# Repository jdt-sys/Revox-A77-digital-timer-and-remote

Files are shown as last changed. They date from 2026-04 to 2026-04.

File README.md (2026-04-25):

# Revox A77 Digital Counter + Web Remote

Adds a digital tape counter and web-based remote control to a Revox A77.  
All mods are reversible and use existing holes where possible.

## Features

- Digital tape counter (OLED display)  
- Web-based remote control (WiFi)  
- Real-time counter updates over WebSocket  
- Safe transport control logic (no rewind → play abuse)  
- Non-invasive install  

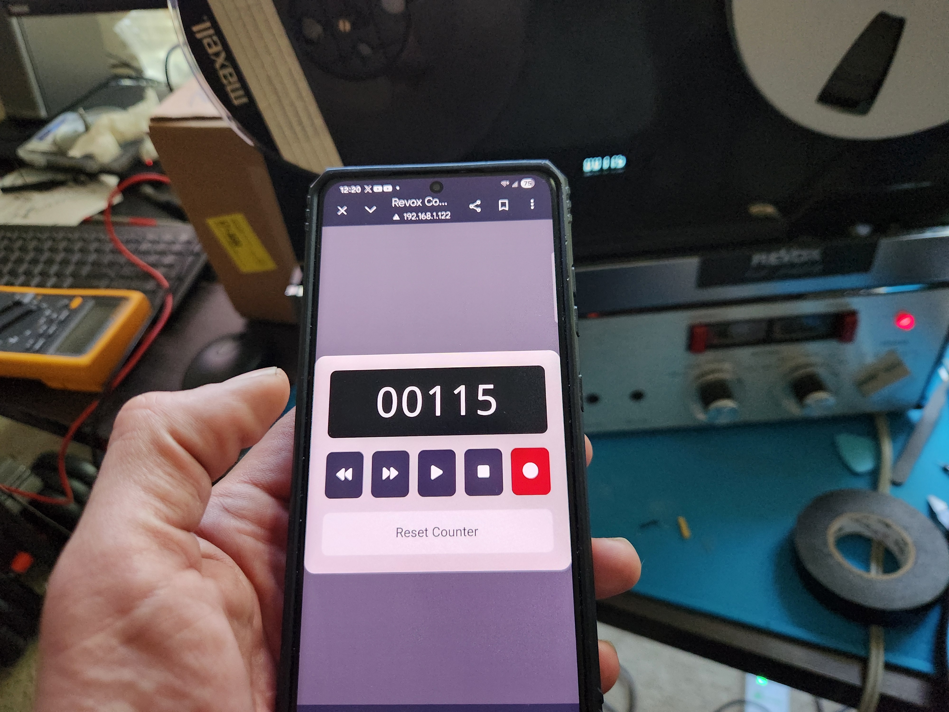
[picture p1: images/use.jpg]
Web UI


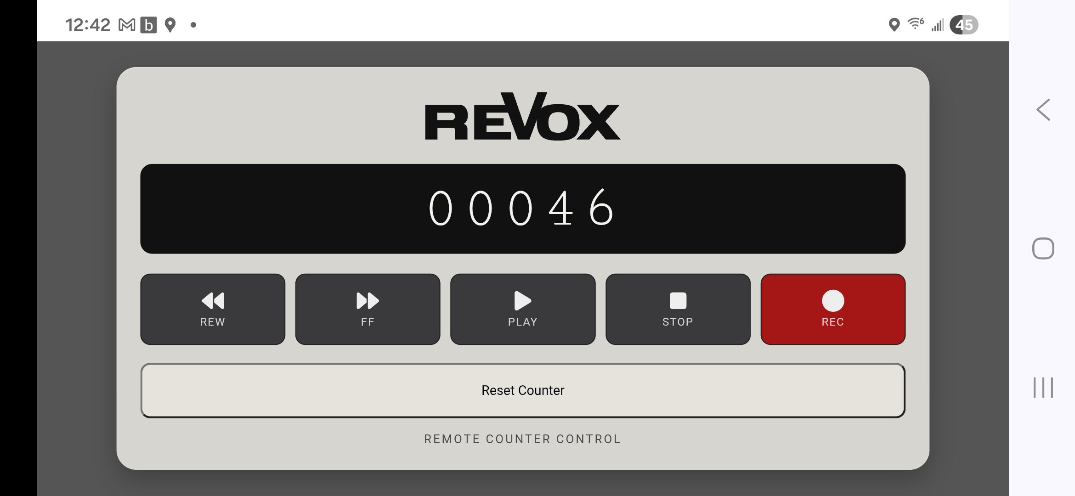
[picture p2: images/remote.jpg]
Remote


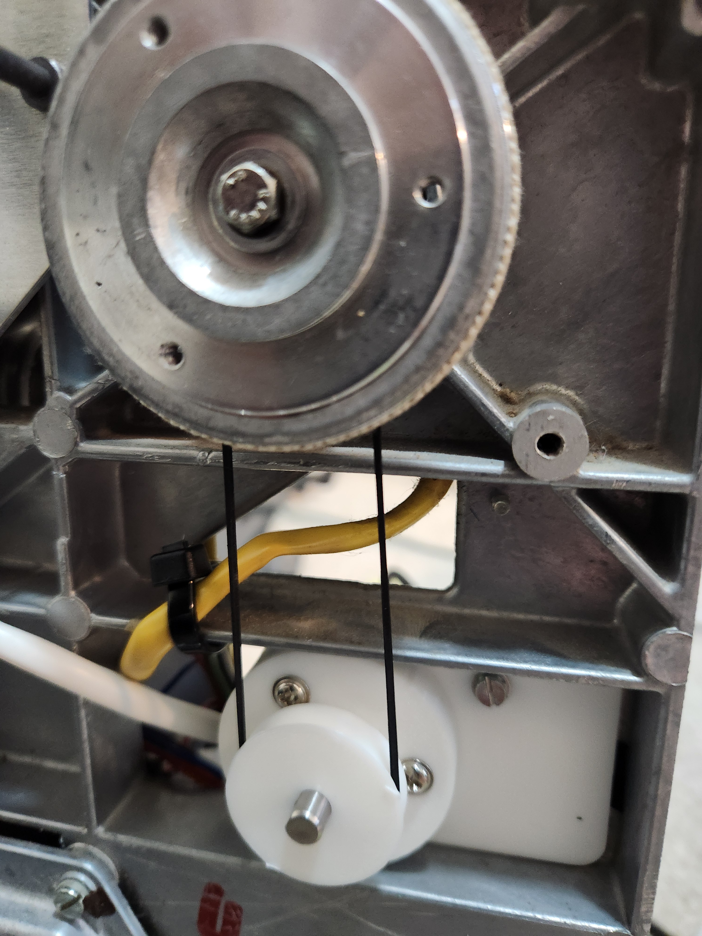
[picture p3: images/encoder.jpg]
Encoder


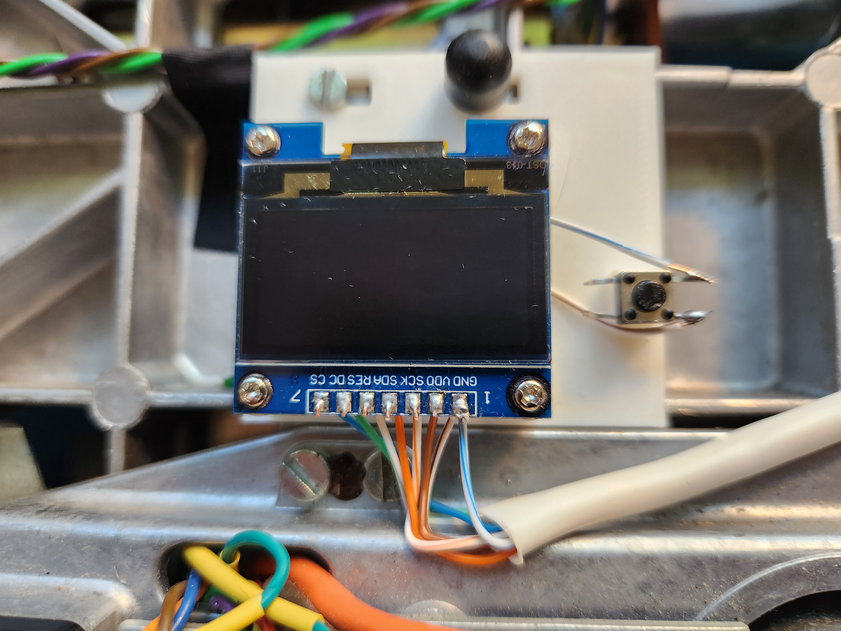
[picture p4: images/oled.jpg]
OLED


## Hardware

- Raspberry Pi Pico W  

- 6-channel 24V relay board with opto-couplers  
  [AliExpress link](https://www.aliexpress.us/item/3256806094499129.html)

- 1.3" SH1106 OLED display  
  [AliExpress link](https://www.aliexpress.us/item/3256806019738729.html)

- Quadrature optical rotary encoder  
  [AliExpress link](https://www.aliexpress.us/item/3256809776375520.html)

- Buck converter (27V → 5V)  
- CAT5 cable (used for OLED + reset button)  

## Transport Control Notes

The A77 remote input will happily switch directly from rewind to play if commanded, which is not kind to tape.

This implementation enforces:

1. STOP  
2. Wait for reels to stop  
3. Then PLAY  

Handled in software to prevent tape abuse.

## Tape Counter

- Quadrature encoder driven from reel  
- PIO-based counting using state machine  
- Software rolling counter + persistence  
- Handles direction changes cleanly  

Future idea:
- “Self-learning” position mapping based on reel size / tape length  

## Software

- MicroPython on Pico W  
- PIO used for encoder counting  
- Async web server (AJAX + WebSocket updates)  
- Custom OLED font rendering

## A77 Remote Wiring

The A77 remote is controlled by shorting specific wires together (via relay contacts).

### Important

Red and brown must be connected for transport functions to latch.  
Without that connection, PLAY / FF / REW will only operate momentarily and won’t stay engaged.

### Connections

- **STOP:** red ↔ brown *(opens to stop / releases latch)*  
- **PLAY:** orange → yellow  
- **FAST FORWARD (FF):** black → gray  
- **REWIND (REW):** white → gray  

### Record (Unverified)

- **REC:** green → blue *(not tested)*  

### Notes

- All control is done by momentarily shorting the corresponding wires.  
- Latching is handled internally by the deck once red/brown are connected.

### References

- https://github.com/peterhinch/micropython-font-to-py — Font encoder
- https://github.com/jamon/pi-pico-pio-quadrature-encoder — PIO-based quadrature decoding  
- https://www.tapeheads.net/threads/revox-a77-wifi-remote-i-am-making-my-own.113867/ — similar DIY WiFi remote project and discussion  

## Repo Contents

- `/src` → MicroPython code  
- `/cad` → 3D printable parts (encoder mount, etc.)  

## TODO

- Clean up wiring at rear of deck  
- Better position tracking (reel size awareness)  

## Disclaimer

You can absolutely break things doing this.  
Double-check voltages, grounds, and relay isolation.

Also:  
Most faults encountered were self-inflicted. Don’t ask me how I know.

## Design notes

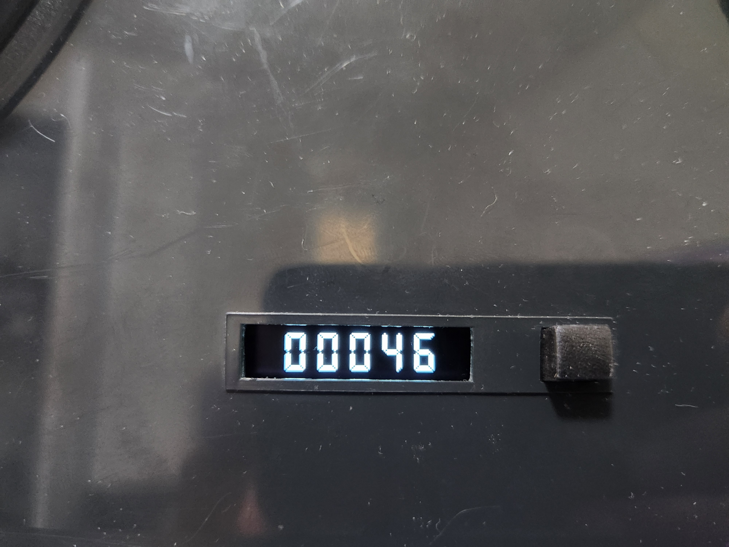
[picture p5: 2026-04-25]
images/counter.jpg

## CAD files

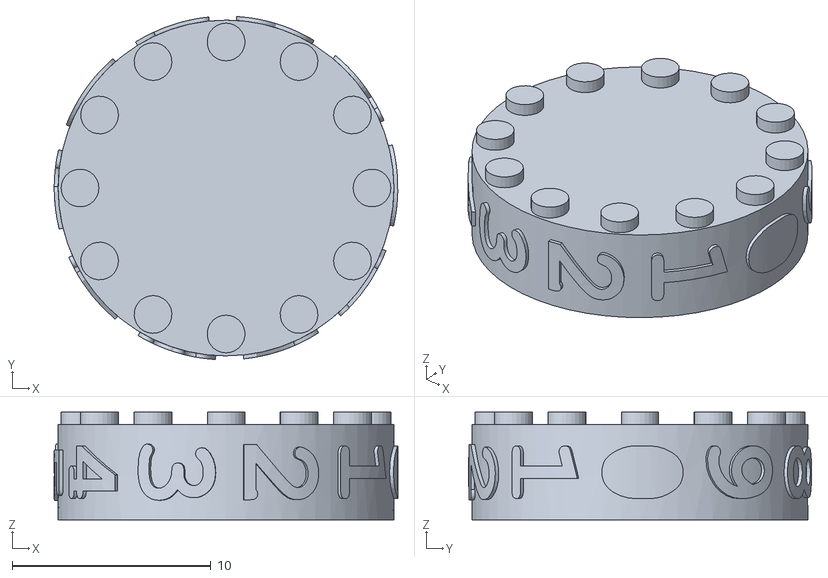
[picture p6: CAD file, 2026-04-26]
cad/wheel2-Fusion.stl
17.3 x 17.3 x 5.43

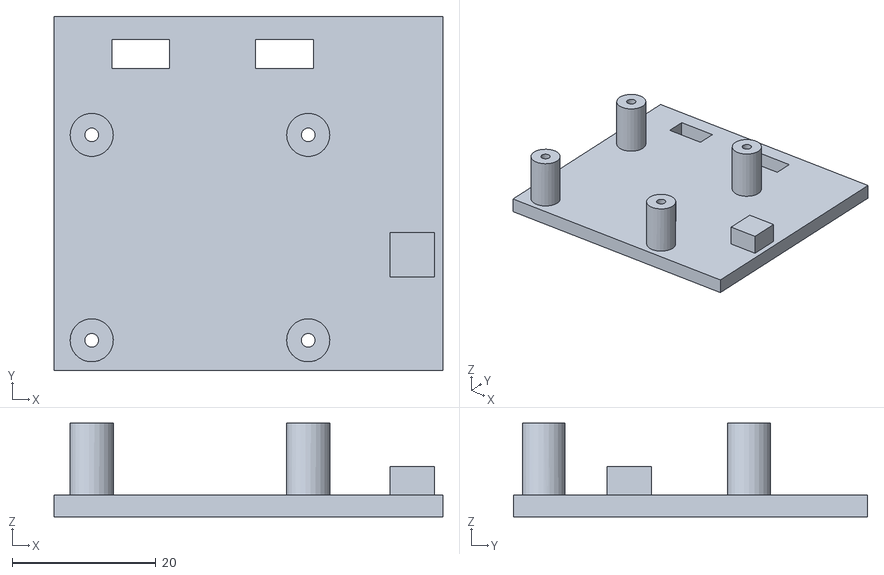
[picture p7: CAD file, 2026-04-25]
cad/reset_holder-Body.stl
54.0 x 49.2 x 13.0

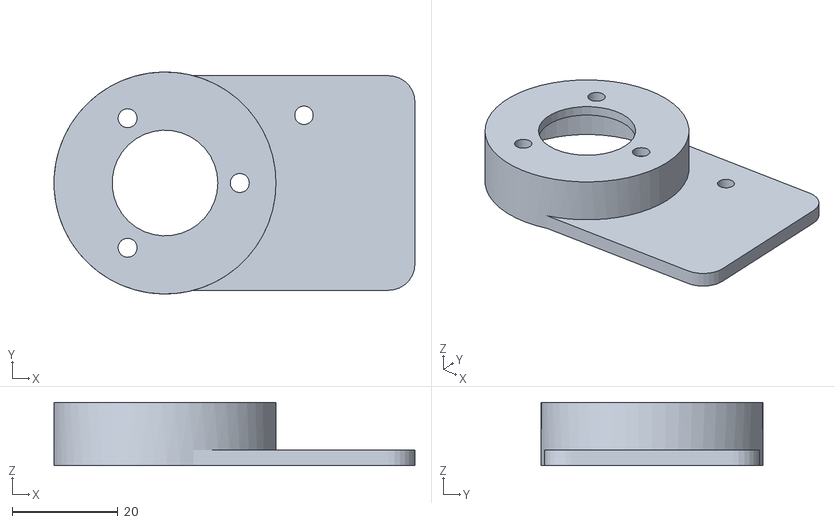
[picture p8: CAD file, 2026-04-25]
cad/encoder_holder-Body.stl
68.3 x 42.0 x 12.0

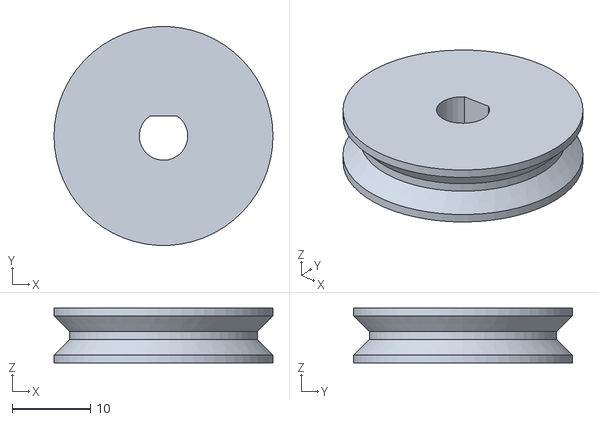
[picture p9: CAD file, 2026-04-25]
cad/encoder_pully-Body.stl
28.0 x 28.0 x 7.00

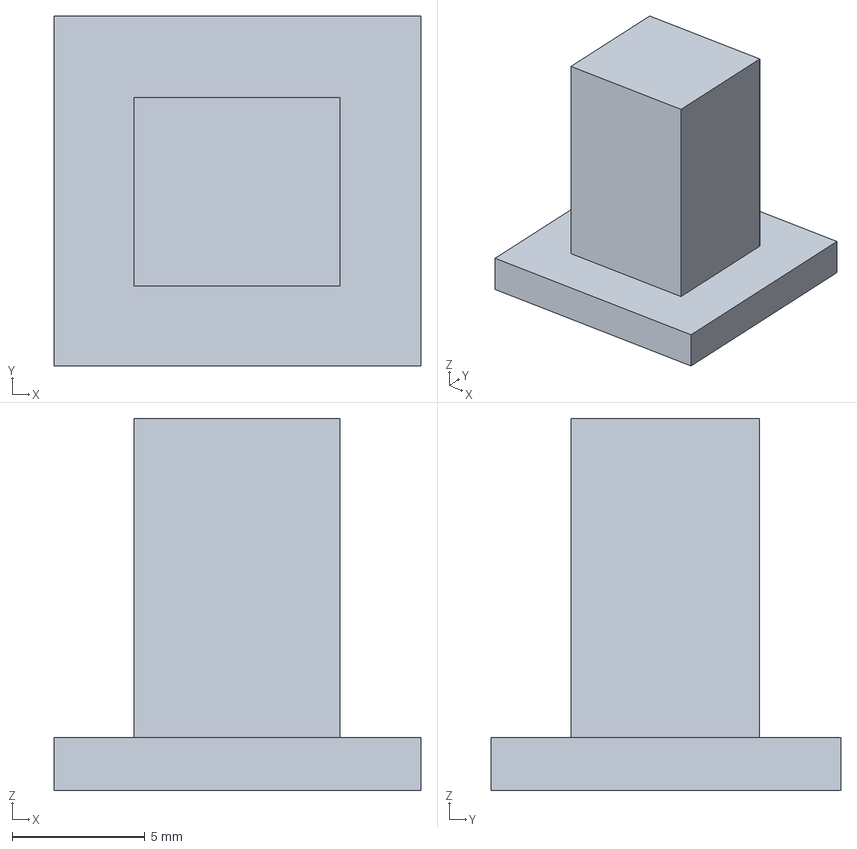
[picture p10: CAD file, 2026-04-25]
cad/reset_stick.FCStd
13.8 x 13.2 x 14.0 mm

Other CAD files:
cad/reset_holder.FCStd
cad/reset_stick-Body.stl
cad/encoder_pully.FCStd
cad/encoder_holder.FCStd

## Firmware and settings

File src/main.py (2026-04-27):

# SPDX-FileCopyrightText: 2022 Jamon Terrell <github@jamonterrell.com>
# SPDX-License-Identifier: MIT

from rp2 import StateMachine
from machine import Pin, SPI
import uasyncio as asyncio
import sh1106
import time

from encoder_pio import encoder, read_raw_count
from display import Display
from counter_websocket import CounterWebSocketServer
from RollingCounter import RollingCounter


ENCODER_CLK_PIN = 14
ENCODER_DT_PIN = 15
RESET_PIN = 16

SPI_ID = 0
SPI_SCK_PIN = 2
SPI_MOSI_PIN = 3
OLED_DC_PIN = 5
OLED_RES_PIN = 4
OLED_CS_PIN = 1

OLED_WIDTH = 128
OLED_HEIGHT = 64

TEXT_X = 18
TEXT_Y = 21

DEBOUNCE_MS = 20
PULSE_MS = 200
WAIT_STEP_MS = 50

WIFI_SSID = "*******"
WIFI_PASSWORD = "******"

TRANSPORT_PINS = {
    "play": 6,
    "stop": 11,
    "rwd": 7,
    "ff": 8,
    "pause": 10,
    "rec": 9,
}


async def main():
    # --- SPI + OLED ---
    spi = SPI(
        SPI_ID,
        baudrate=10_000_000,
        polarity=0,
        phase=0,
        sck=Pin(SPI_SCK_PIN),
        mosi=Pin(SPI_MOSI_PIN),
    )

    oled = sh1106.SH1106_SPI(
        OLED_WIDTH,
        OLED_HEIGHT,
        spi,
        Pin(OLED_DC_PIN),
        Pin(OLED_RES_PIN),
        Pin(OLED_CS_PIN),
    )

    display = Display(oled, OLED_WIDTH, OLED_HEIGHT, TEXT_X, TEXT_Y)

    # --- PIO Encoder ---
    sm = StateMachine(
        1,
        encoder,
        freq=125_000_000,
        in_base=Pin(ENCODER_CLK_PIN),
        jmp_pin=Pin(ENCODER_DT_PIN),
    )
    sm.active(1)

    # --- Reset button ---
    reset_btn = Pin(RESET_PIN, Pin.IN, Pin.PULL_UP)

  
    # --- Transport GPIO setup ---
    transport_gpio = {
        name: Pin(pin_num, Pin.OUT, value=0)
        for name, pin_num in TRANSPORT_PINS.items()
    }

    # --- Web interface ---
    web = CounterWebSocketServer(WIFI_SSID, WIFI_PASSWORD, title="Revox Counter")

    state = {
        "last_text": "",
        "last_btn": reset_btn.value(),
    }

    def refresh_counter():
        raw = read_raw_count(sm)
        counter.update(raw)
        counter.tick()

    def update_outputs():
        text = counter.formatted()
        if text != state["last_text"]:
            print(text)
            display.draw(text)
            web.set_text(text)
            state["last_text"] = text

    def service_counter():
        refresh_counter()
        update_outputs()

    def pulse_pin(pin, ms=PULSE_MS):
        print("-> mapped to GPIO:", pin)
        print("-> initial value:", pin.value())

        print("-> setting HIGH")
        pin.on()
        print("-> value now:", pin.value())

        time.sleep_ms(ms)

        print("-> setting LOW")
        pin.off()
        print("-> value now:", pin.value())

    def stop_transport_if_moving():
        moving = counter.counterMovedInLastSecond()
        print("playing =", moving)

        if not moving:
            return

        stop_pin = transport_gpio.get("stop")
        if stop_pin is None:
            print("-> STOP pin missing")
            return

        print("stop first")
        pulse_pin(stop_pin)

        while counter.counterMovedInLastSecond():
            print("waiting..")
            service_counter()
            time.sleep_ms(WAIT_STEP_MS)

    def on_transport(cmd):
        print("\n=== TRANSPORT EVENT ===")
        print("cmd:", cmd)

        if cmd == "reset":
            print("-> RESET requested")
            counter.reset()
            update_outputs()
            print("=== DONE ===\n")
            return
        
        
        if cmd.startswith("goto:"):
            target = int(cmd.split(":")[1])
            print(f"-> GOTO requested: {target}")
            counter.goto(target)
            print("=== DONE ===\n")
            return

        pin = transport_gpio.get(cmd)
        if pin is None:
            print("-> UNKNOWN COMMAND (ignored)")
            print("=== DONE ===\n")
            return

        if cmd != "stop":
            stop_transport_if_moving()

        pulse_pin(pin)

        print("=== DONE ===\n")
        


    # --- Counter logic ---
    counter = RollingCounter(steps_per_count=300, on_transport=on_transport)


    web.set_transport_callback(on_transport)
    await web.start()

    while True:
        service_counter()

        # --- Button debounce ---
        btn = reset_btn.value()
        if state["last_btn"] == 1 and btn == 0:
            await asyncio.sleep_ms(DEBOUNCE_MS)
            if reset_btn.value() == 0:
                counter.reset()
                print("Physical reset")
                update_outputs()

        state["last_btn"] = btn

        await asyncio.sleep_ms(10)


asyncio.run(main())

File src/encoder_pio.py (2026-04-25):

# SPDX-FileCopyrightText: 2022 Jamon Terrell <github@jamonterrell.com>
# SPDX-License-Identifier: MIT
# https://github.com/jamon/pi-pico-pio-quadrature-encoder/


from rp2 import asm_pio

@asm_pio(autopush=True, push_thresh=28)
def encoder():
    wrap_target()

    wait(0, pin, 0)
    jmp(pin, "clk_low_data_high")

    mov(x, invert(x))
    jmp(x_dec, "inc1")
    label("inc1")
    mov(x, invert(x))

    label("clk_low_data_high")
    jmp(x_dec, "dec1")
    label("dec1")

    wait(1, pin, 0)
    jmp(pin, "clk_high_data_high")

    jmp(x_dec, "dec2")
    label("dec2")

    label("clk_high_data_high")
    mov(x, invert(x))
    jmp(x_dec, "inc2")
    label("inc2")
    mov(x, invert(x))

    wrap()


def read_raw_count(sm):
    sm.exec("in_(x, 28)")
    return sm.get()

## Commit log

2026-04-25 Document A77 remote wiring and control connections
    Added section about A77 remote wiring and connections.
2026-04-25 Revise hardware section in README
    Updated hardware list with new relay board and display links.
2026-04-25 Update control notes in README
    Removed recommendations for switching modes and using relays.
